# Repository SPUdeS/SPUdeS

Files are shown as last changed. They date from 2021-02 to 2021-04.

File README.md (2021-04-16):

<div id="SPUdeS">
    <h1>
         <span>
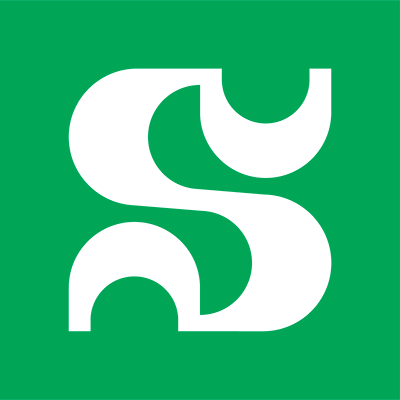
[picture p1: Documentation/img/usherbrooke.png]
usherbrooke
            
         </span>
         SPUdeS
    </h1>
    <h3>Stewart Platform Université de Sherbrooke</h3>
    <h3>UdeS-GRO | 65<sup>th</sup> Promotion | 2021</h3>
</div>

[//]: # (------------------------------------------------)

<div id="badges">
    

 

</div>

[//]: # (------------------------------------------------)

**SPUdeS is a six degrees of freedom Stewart Platform. 
This is an academic project by robotics engineering undergraduates at l'Université de Sherbrooke.**

<!-- TODO: Change image to be smaller and add a real image of platform -->
<div id="platform" align="center">
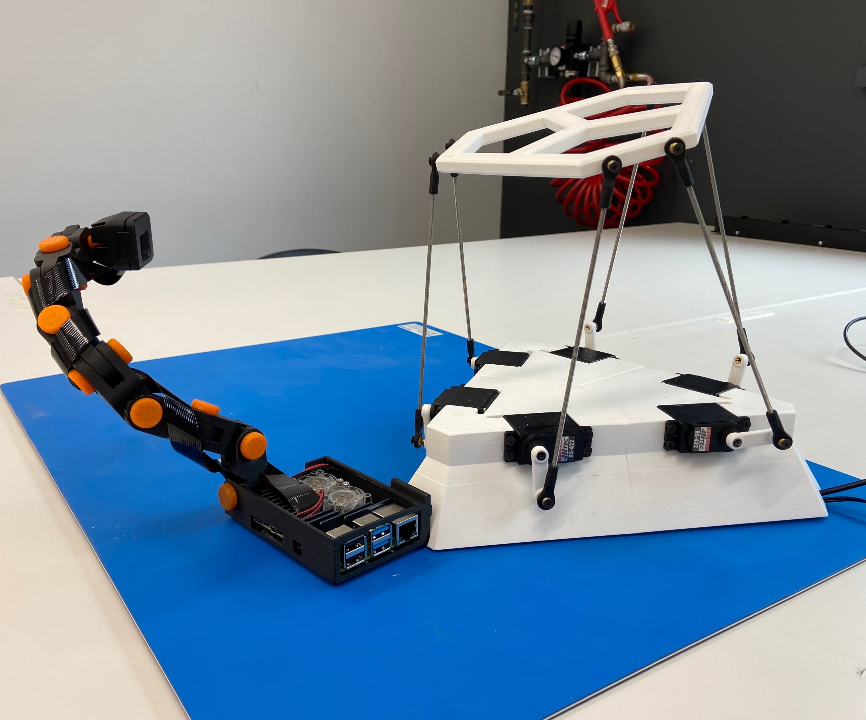
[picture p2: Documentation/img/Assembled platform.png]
Platform Assembly
    
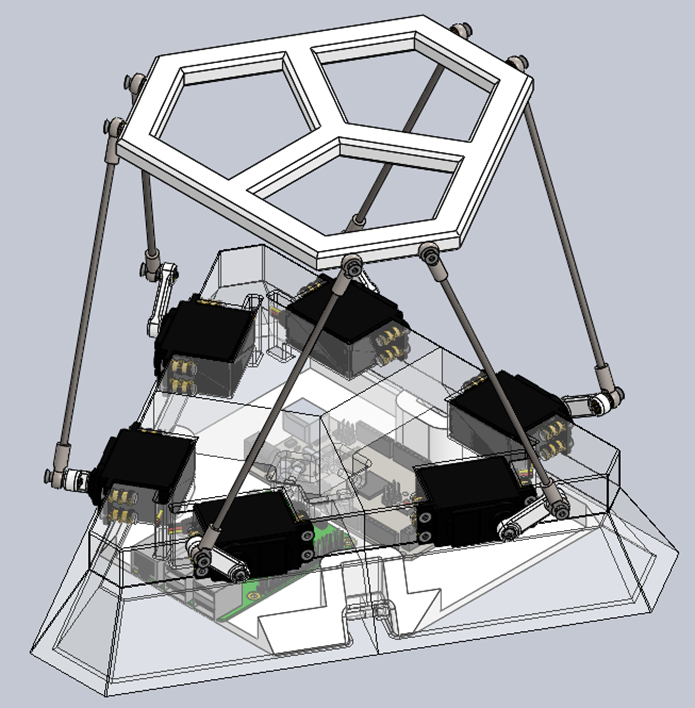
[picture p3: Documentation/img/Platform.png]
Platform Assembly
    
</div>

## Table of Contents
- **[Stewart Platforms](#Stewart)**
- **[Setup](#Setup)**
- **[Supplies](#Supplies)**
    - **[Single-Board Computer](#Computer)**
    - **[Microcontroller](#Controller)**
    - **[Servomotors](#Servo)**
    - **[Power Adaptor](#Power)**
    - **[Threaded Rods](#Rods)**
    - **[Heim Joints](#Joints)**
    - **[Hardware](#Hardware)**
    - **[Parts to solder](#Parts_solder)**
    - **[Parts to print](#Parts_print)**
- **[Platform Assembly Guide](#Assembly)**
    - **[Design](#Design)**
    - **[CAD Files](#CAD)**
    - **[Platform](#Platform)**
    - **[Base](#Base)**
    - **[Servo motor arms](#Servo)**
    - **[Legs](#Legs)**
    - **[Microcontroller holder](#Holder)**
    - **[Summary](#Summary)**
- **[Electrical Connection Guide](#Electrical)**  
  - **[Protoboard Soldering](#Proto)**
  - **[Soldering Recommendations](#Soldering)**
- **[Software Installation Guide](#Software)**
  - **[Machine requirements](#Machine_requirements)**
  - **[Cloning the Repository](#Cloning_the_Repository)**
  - **[Installing the requirements](#Installing_the_requirements)**
  - **[Running the server](#Running_the_server)**
- **[Arduino Setup Guide](#Motor_control)**
  - **[Arduino Communication Protocol](#Coms)**
  - **[PWM Precision](#PWM)**
- **[User Interface](#Operation)**
  - **[Camera](#Camera)**
  - **[Input](#Input)**
  - **[Graphical Representation of the Platform](#Graph)**
- **[License](#License)**  
 
[//]: # (------------------------------------------------)

## Stewart Platforms
A Stewart platform is a type of parallel robot built in such a way as to offer six degrees of freedom. 
This type of platform was created and publicised in the second half of the 20th century by three different engineers. 
Distributing the load on six legs allows for a strong manipulator while preserving high precision in movements. 
The combination of high strength and precision in six degrees of freedom makes this type of robot the ideal platform for various simulators (automobile, aviation). 
This type of robot as also been used for a telescope and tire testing machines.

Fundamentally, the platform is built from six linear actuators in parallel. 
Each ends of the linear actuators are linked to the fixed base and the manipulator via Heim joints. 
It is also possible to assemble the platform with rotary actuators. 
The rotation of an arm connecting to the base of the leg allows for some variation of the effective length of the legs emulating a linear actuator.
It is the way we have decided to build our prototype platform since servo motors are cheaper and easier to get our hands on then linear actuators.

## Setup
1. Acquire the components in the **[Supplies](#Supplies)** section.
2. If needed, adapt the [CAD models](CADs) of the [base](CADs/Base.SLDPRT), the [platform](CADs/Platform.SLDPRT) and the [servo arms](CADs/Legs.SLDASM) to your specific dimensions.   
2.1. If you modified the [CAD models](CADs) regenerate the [3D printing files](CADs/V2%-%HS422/3D%printing%files).
3. 3D print the platform using the [3D printing files](CADs/V2%-%HS422/3D%printing%files). This may take several days.
4. Follow the **[Platform Assembly Guide](#Assembly)** to assemble the 3D printed parts. This requires the **[Supplies](#Supplies)**.
5. Follow the **[Electrical Connection Guide](#Electrical)** to solder the protoboard.
6. Follow the **[Software Installation Guide](#Software)** to set up the server and the user interface.
7. Follow the **[Arduino Setup Guide](#Motor_control)** guide to upload the [``StandardFirmata.ino``](SPUdeS/Arduino/StandardFirmata/StandardFirmata.ino) file to the Arduino.
8. Set up the *[Raspberry Pi](#Computer)* or a computer by connecting it with the *[Arduino](#Controller)*, your computer and to a power source.
9. Commands can be sent to the platform using the user interface. Refer to the **[User Interface](#Operation)** section for more information.

## Supplies
### Single-Board Computer
- Brand: *[Raspberry Pi](https://www.raspberrypi.org/products/raspberry-pi-4-model-b/)*
- Model: Raspberry Pi 4 Model B
- Quantity: 1

### Microcontroller
- Brand: *[Arduino](https://store.arduino.cc/mega-2560-r3)*
- Model: Mega 2560 REV3
- Quantity: 1

### Servomotors
- Brand: *[Hitec RCD](https://hitecrcd.com/products/servos/sport-servos/analog-sport-servos/hs-422/product)*
- Model: HS-422
- Quantity: 6

### Power Adaptor (5V, 6A)
- Brand: *[CUI Inc.](https://www.digikey.com/en/products/detail/cui-inc/SWI10-5-N-P5/6618696)*
- Model: SWI10-5-N
- Quantity: 1

###  Threaded Rods
- Brand: *[uxcellM3](https://www.amazon.ca/gp/product/B01M9D4ASU/ref=ppx_yo_dt_b_asin_title_o08_s00?ie=UTF8&psc=1)*
- Model: a16071500ux0035
- Quantity: 6

###  Heim Joints
- Brand: *[Que-T](https://www.amazon.ca/gp/product/B08217LDWH/ref=ppx_yo_dt_b_asin_title_o07_s00?ie=UTF8&psc=1)*
- ASIN: B08217LDWH
- Quantity: 12

###  Hardware
-	Threaded inserts M3 x 6mm (42x; optional)
-	Countersunk bolts M3x6 (6x; optional)
-	Countersunk bolts M3x12 (42x)
-	Nylock nuts M3 (6x)
-	Round head self-tapping screws No3 (6x)

###  Electrical Parts
- Proto-board (1x)
- Pin / Female headers (6x)
- Wires 
- Soldering iron and solder
     
###  Parts to print
There are four parts to print: the [platform](CADs/V2%20-%20HS422/Platform.SLDPRT), 
the [base](CADs/V2%20-%20HS422/Base%20V3.SLDPRT), 
the [microcontroller holder](CADs/V2%20-%20HS422/MicroController%20Holder.SLDPRT) 
and the [servo arms](CADs/V2%20-%20HS422/ServoArm.SLDPRT). 
Materials needed:
- A spool of PLA
- Access to a 3D printer

## Platform Assembly Guide
### Design
The main components of the robot are the base, the arms fixing the legs to the servo motors, the legs themselves, and the platform. 
The geometry and proportions of the platform are critical factors allowing the position of the manipulator to be completely defined. 
Furthermore, using rotary actuators elevate the complexity versus using simple actuators. 
Thankfully, Robert Eisele has proposed and published a solution for the inverse kinematics of the platform using rotary actuators. 
Building from his *[work](https://www.xarg.org/paper/inverse-kinematics-of-a-stewart-platform/)*, it is possible to develop a custom sized platform given we respect some parameters. 
For those of you who would want to change the values we used be sure to look at the parameters defined in the configuration files of the project. 
We would strongly advise also trying your new parameters in the CAD files to inspect proportions and overall look. 
We have drawn them based on variables to make it easy for the user to input whatever values desired for the basic parameters.

To keep the project as simple as possible, we have designed the platform to be table-top sized. 
This way, it is not too small so that the hardware is easily available at the hardware store. 
On the other hand, it is not too big, so the cost of material isn’t prohibitive either. 
For maximum flexibility we based all our design on the fact that a 3D printer was readily available. 
One could use other ways to build the platform out of different materials, but we felt 3D printing was the more practical means of fabrication for most.

### CAD Files
First of all, you’ll find two version of the platform. The version one being a prototype with smaller servo motors. 
We’ve moved on from that design to upgrade to [better motors (HS-422 model)](CADs/V2%20-%20HS422). 
Those motors are more powerful limiting the impact of friction in the Heim joints at both ends of the legs. 
Note that the [CAD files of the first version](CADs/V1%20-%20SG90%20-%20Deprecated) aren’t based on variables lengths and dimensions aren’t defined the same way as the second version. 
This is important since the values in the configuration file of the main program are based on the second version’s way of dimensioning the platform. 
A reader that would want to build the first platform would have to manually measure (in the CAD software) some of the variables to update the [``configuration files``](SPUdeS/Platform/config.py) variables. 
As stated earlier, the brass inserts are optional. But if not using them, don’t forget to adjust the size of the holes where bolts will be threaded. 
Using M3 bolts, we’d recommend holes about a quarter to half a millimeter less in diameter to allow the thread to grip well on the plastic. 
The exact size depends on the precision of the printer used and orientation of the print; this I just a recommendation and testing should be done before hand.

### Platform
The word platform in its general sense describes the project in whole (Stewart Platform). 
But we also use the term to refer specifically to the upper part of the robot. 
It is a way to distinguish it from the base and the legs. 
[The platform](CADs/V2%20-%20HS422/Platform.SLDPRT) is one of the simplest parts of the project. 
It is also one that allows for lots of customization. 
This piece could be redesign to whichever shape is desired while keeping in mind that the more weight is added at the top, the greater the load placed on the servos is. 
The only other thing to keep in mind would be to try keep the anchors in the general vicinity of the anchors of the base. 
That way, in the home position, the legs are as upright as possible and allow for better movement. 
The usage of rotary actuators to lift the legs up creates a plane in which the servo arms operate. 
Since the [Heim joints](CADs/V2%20-%20HS422/Rod%20End) have an angular limit on the movement they allow, starting with upright legs effectively put the interior portion of the join at 90 degrees to the leg itself and allows for the greatest range of motion.

Printing the model provided needs no support and will take about 4 hours. 
This time is only provided as an indication since lots of parameters can impact the printing time (we used a standard layer height of 0.20 mm, 3 horizontal walls, 4 vertical walls and a 15% gyroid infill). 
For the assembly it is really simple, only install the threaded inserts press-fit in the six anchor holes. 
This is where the upper part of each leg will attach. Note that inserts are optional as stated earlier, but don’t forget to resize the anchor holes properly. 

### Base
[The base](CADs/V2%20-%20HS422/Base%20V3.SLDPRT) is the longest part to print and the more complex part of the build. 
Most of the assembly starts here and the operation of the platform is heavily linked to the geometry of this part. 
That is to says, if the platform is a part which allows for creativity, the base isn’t so much. 
For someone who would like to play with the fundamental geometry of the base we’d strongly advice to look attentively at the paper provided in reference (solution for the inverse kinematics of a servo motor operated Stewart platform by Robert Eisele). 
For others that would only like to resize the project, this is facilitated by the variables included in the CAD files. 
Note that the measurements of the motors are also variables, so it is also possible to change the motors for bigger or smaller projects without having to redraw the base. 
Just don’t forget to adjust the value of the parameters contained in the configuration file so the computation is accurate for your new dimensions. 
The printer used for our version was the Pruas Mini+ which has a build volume of 18 cm x 18 cm x 18 cm, for this reason the base is [split in three parts](CADs/V2%20-%20HS422/Base%20V3-Split.SLDPRT). 
The undivided part is also available for people using printers with bigger build volumes or is downsizing the platform results in not enough space to bolt the different pieces together. 
We suggest printing the parts up-side down. 
Leveraging the draft angle of the design and the overhang capabilities of the printer to our advantage to reduce support to its minimum saves more then an hour per piece (a third of the base). 
If your bridging parameters are well dialed-in, the part can be printed as is in the upside-down orientation. 
Otherwise, the part needs some supports that you can apply to the faces where the servo motors lie. 
Since there’s minimal support needed, the print time added is negligeable and we’d suggest taking this route since in the end the surface will look better, and it is probably not worth risking disappointing surface finish only to save couple of minutes on a ten plus hours print. 
With three walls and the rest of the parameters the same, it takes about 30-32 hours in total to complete printing the base. Don’t forget to resize holes if not using the inserts.

To assemble the platform, follow those steps:
1.	Fix the three parts of the base together with the M3x16 mm bolts (6) and the nylon locknuts (6). Holes for the bolts and to fix the nut in place are located underneath the base. \
&nbsp;&nbsp;&nbsp;&nbsp;&nbsp;&nbsp; a.	Be sure to tighten enough so that the parts do not have room to move relative to each other.\
&nbsp;&nbsp;&nbsp;&nbsp;&nbsp;&nbsp; b.	The nut may start to turn within the hexagonal hole where it’s located because of the friction of the nylon transferring the torque of the bolt. Wedging a small flat head screwdriver or a small Exacto blade helps retain the nut in place while tightening the bolt.
2.	Install the inserts that allow for the servos to be fixed. Note that four inserts are more then required for the application but since we had them, and the servo used had four holes to fix them we used them all. This is not optimal in any way nor is it required.
3.	Pass the wires of the servo motors through the holes in the base and slide the motors in place.
4.	Install the bolts to fix the servos.

### Servo motor arms
The [servo arms](CADs/V2%20-%20HS422/ServoArm.SLDPRT) are the parts that requires the less time for the print and are simple to assemble. 
The bridging parameters will impact the looks of one side of the arm, printing toothed side-down will allow the better-looking side to be facing out at installation (surface irregularities due to the bridging end up on the base-facing side of the arm). 
Printing the 6 servo arms at once will only take about one hour. 
We advise using the same general parameters but increasing the number of walls (increasing the infill percentage doesn’t have as much impact). 
That way, the arms are sturdier and print time isn’t that much longer. 
Once printed, install the threaded insert in the round hole, then install the toothed side onto the servo motor shaft. Do not push hard on the shaft towards the servo motor, it could damage the motors. 
Instead, put the arm in place and gently screw it in place. The self-tapping screw will thread into the plastic shaft pulling the arm on its way. 
When placing the arms, be sure that the range allowed by the servos (about 180 degrees) span the bottom to the top of the base and faces the exterior. 
This allows the leg to have a full range of motion from the lower point to the highest point of the arc made by the rotation of the arm. 
In the configuration used we like the arms to be outside facing but inside would be another working configuration (all arms must be the same in one or the other configuration).

### Legs
The legs are simply the [female Heim joints](CADs/V2%20-%20HS422/Rod%20End) threaded at both ends of the [150 mm rods](CADs/V2%20-%20HS422/Tige%20filetée.SLDPRT). 
Be sure to them facing approximately in the same direction so that the range of motion isn’t hampered. 
Then it is just a question of fixing the legs to both the base and the platform using the M3 blots. 
The major triangle in the base and the platform should be inverted as shown in the image. 

### Microncontroller holder
The positioning of the microcontrollers is up to you. 
The [holder](CADs/V2%20-%20HS422/MicroController%20Holder.SLDPRT) piece doesn’t have holes in it. 
Depending on the type of different microcontroller used to drive the platform, bolt patterns may vary. 
For this reason, we suggest marking drilling holes at the location you want to place the microcontrollers on the holder. 
Then it is only a question of installing the inserts (drill a hole smaller than the insert diameter to allow for a press-fit in the plastic) and using small M3x6 mm bolts to fix the microcontrollers. 
The holder should snap in place beneath the base. 

### Summary
Printing all the pieces required for the build takes about 560 grams of PLA which is a bit more than half a spool. 
Accounting for three quarters to an entire spool’s (1 kg) worth of PLA is advisable for someone who’d want to do tests to optimize surface finish. 
The pictures shown below illustrate how the principal components are fastened to the platform (in this case, the base is in one piece but the three-pieces model is assembled in the same way).

<div id="platform" align="center">
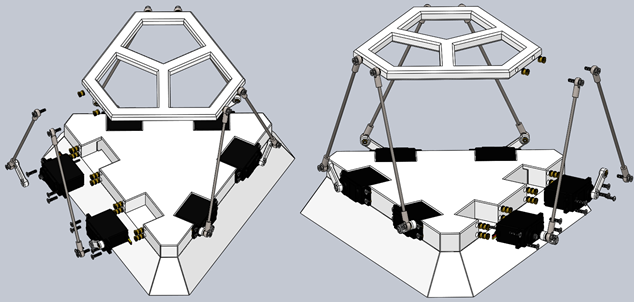
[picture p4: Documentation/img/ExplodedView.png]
    
</div>

Now it is only a question of uploading the codes to the Arduino and the raspberry pi and connecting both with the appropriate power adaptors. 
Launching the web server allows for a clean interface where the user can command the platform.

## Electrical Connection Guide
### Protoboard Soldering
This section makes reference to the [electrical schematics](Documentation/Electical%20schematics.pdf).The electrical part of the assembly requires you to solder a protoboard. 
-	Solder two female pin headers to the protoboard. This will be used for the power supply by connecting two male connectors; one for the ground and one for the VCC.
-	Solder 6 short wires to the protoboard’s positive (VCC) side. These will be used on the positive side of each motor.
-	Solder 7 short wires to the protoboard’s ground side. These will ground each motor and the Arduino.
-	Each of the motors will need an additional wire to plug into the digital pin of the Arduino. 

<div style="text-align: center;">
  <table style="margin: 0px auto">
    <tr>
      <td> Motor 1 </td>
      <td> Motor 2 </td>
      <td> Motor 3 </td>
      <td> Motor 4 </td>
      <td> Motor 5 </td>
      <td> Motor 6 </td>
    </tr>
    <tr>
      <td> Pin 7 </td>
      <td> Pin 9 </td>
      <td> Pin 11 </td>
      <td> Pin 12</td>
      <td> Pin 5 </td>
      <td> Pin 3 </td>
    </tr>
  </table>
</div>

### Soldering Recommendations	
The motor positioning is important so be careful when plugging them. Here are some tips you can use:
-	Soldering will be simpler if you minimise the distance between the components.
-	Be careful to not touch the protoboard.
-	It can be useful to use more solder than usual.

## Software Installation Guide
The interface was build using the Python micro framework Flask. We built our webpage using html and handle our requests by using Javascript functions and route handling on the server side.
###  Machine Requirements
Our project runs on specific versions of Python:
- [``Python 3.7``](https://www.python.org/downloads/release/python-3710/)
- [``Python 3.8``](https://www.python.org/downloads/release/python-389/)
- [``Python 3.9``](https://www.python.org/downloads/release/python-394/)

[``pip3``](https://pip.pypa.io/en/stable/) is also required to install the project's various packages.
### Cloning the Repository
Let us start the installation by cloning the repository. 
You may choose to do this via the Github Desktop App or through some code versioning software such as Sourcetree or Square Desktop. We will use Git in a terminal. 
If you haven't already, download [``Git``](https://git-scm.com/downloads).
Start by entering into the folder you want the project to be in and open up a terminal. Next use the following command to clone the repository.
```shell
git clone https://github.com/SPUdeS/SPUdeS.git
```
### Installing the requirements
Now you will need to install the modules and packages needed to run the server. Go ahead and run this next command.
```shell
pip3 install -r requirements.txt
```
The [``requirements.txt``](requirements.txt) file is what lets you download all the dependencies for the project.
If you get an error where an import is missing, please install it manually. For example, to download OpenCV manually you will open back up that terminal window and write the following.
```shell
pip3 install opencv-python
```
If you are using a Raspberry Pi and are still having issues with OpenCV, *[this link](https://stackoverflow.com/questions/53347759/importerror-libcblas-so-3-cannot-open-shared-object-file-no-such-file-or-dire)* may be helpful.
### Running the server
Starting from the root of the repository, run the server with this command.
```shell
python3 SPUdeS.py
```
To see the interface webpage visit *[this address](http://127.0.0.1:5000)* on the same machine: ``http://127.0.0.1:5000`` 

## Arduino Setup Guide

### Arduino Communication Protocol
To control the servo motors, we use a microcontroller, the *[Arduino Mega 2560](#Controller)*. 
Since the angles we need to send to the servos are calculated in our inverse kinematics python code, we chose to communicate directly from a python program to the Arduino. 
This is done using the open source *[pyFirmata library](https://github.com/tino/pyFirmata)*, which applies the *[Firmata protocol](https://github.com/firmata/protocol)* for communication with microcontrollers. 
To use this protocol, we simply need to send the [``StandardFirmata.ino``](SPUdeS/Arduino/StandardFirmata/StandardFirmata.ino) file to the Arduino and import the pyFirmata library into our program.

We created a class, [``ard_communication``](SPUdeS/Arduino/ard_communication.py) that applies this concept. 
There are two ways to use it, the first being to simply run it and use its functions in the main, a way that was mostly used to test the motor movements with preprogrammed trajectories and manual inputs. 
The second way is to initialize an instance of the class in our server, and then use its functions there, as we did with our end to end project. 
Its main function is setServoAngle, which receives an array of n arrays of 6 angles, one for each motor. 
It can take angles in degrees and radians, depending on the parameter isRad, which will make sure to correct the angles so they are sent in degrees to the Arduino.

For now, the class uses the digital pins of the Arduino in their pyFirmata.SERVO mode, which makes it so we can send angles in degrees to the Arduino, and it will convert it to a corresponding voltage in PWM to the servos. 
This has some drawbacks, such as a loss in precision of the angles since the digital.write function requires integer values. 
Also, the discretization of the trajectory can look somewhat choppy because the program needs to sleep for a certain amount of time before sending a new angle, otherwise it will miss some waypoints.

### PWM Precision
This brings us to the next step for the motor control aspect of the project. 
There is a possibility to change the digital pins' mode to pyFirmata.PWM and change the file uploaded to the Arduino with a modified version of 
example file *[simpleAnalogFirmata](https://github.com/grappendorf/arduino-framework/blob/master/Firmata/examples/SimpleAnalogFirmata/SimpleAnalogFirmata.ino)*. 
[Our implementation of this file](/SPUdeS/Arduino/PWMFirmataBeta/PWMFirmataBeta.ino) was still in beta and not ready for use with our [ard_communcation](SPUdeS/Arduino/ard_communication.py) module. 
The goal of these changes is to change from an 8 bit resolution PWM to a 16 bit resolution PWM and get rid of the integer restriction of the digital.write function. 
With a few changes, this could allow much more precision in the platform's movements, but might reduce the refresh rate of the PWM, which could cause other issues. 
It is still the next step for motor control since precision is crucial for a Stewart's platform. 
Though it was not needed yet for our implementation of the platform since it currently has no real function and the standard Firmata file with the SERVO mode for the Arduino's pins are enough for our proof of concept.

## User Interface
The user interface (UI) is implemented using [this html file](SPUdeS/PythonUI/templates/index.html). 
We used *[Bootstrap](https://getbootstrap.com)* to format the webpage and Javascript to handle requests.
The user interface can be split into three main parts:
- The Camera
- The User Input
- The Graphical Representations of the Platform

<div align="center">
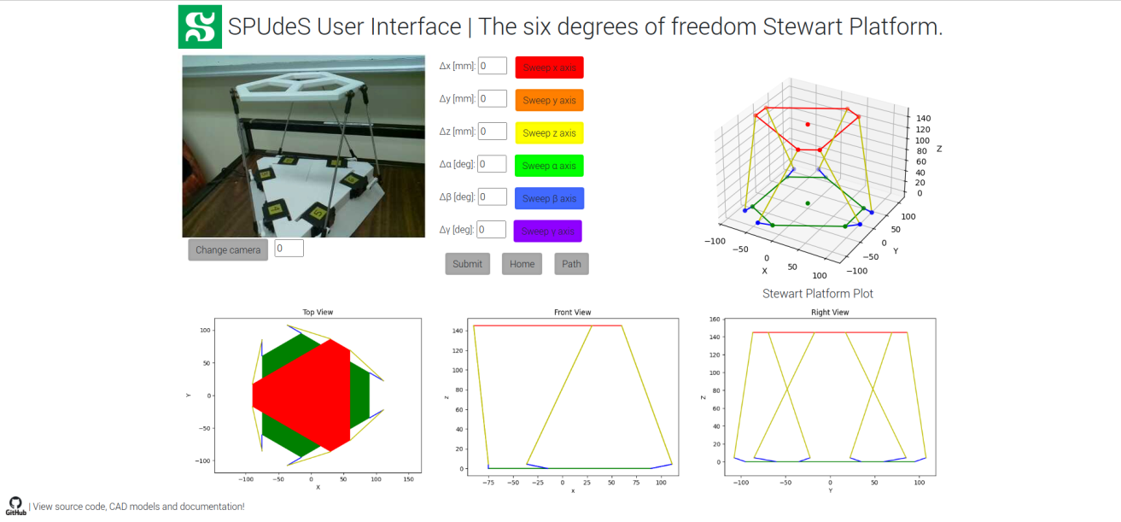
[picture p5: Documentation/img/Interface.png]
Interface
    
</div>

### Camera
The camera was implemented to show the platforms movements live through the UI. 
We used *[OpenCV](https://opencv.org)* to implement the live video feed.
We have tested the use of a laptop webcam and a Raspberry Pi camera. Both have worked 
successfully. There is a button and input that allow you to change the port of the 
camera being used. 

<div align="center">
  CameraButton
</div>

### User Input
Firstly we have inputs for specific positions of different axes possible. 
To use these enter a value in as many of the boxes and hit the button Submit. 
This sends the request to the server to sent to the platform and the update of the graphs. 
Secondly we have the sweep buttons for each axis. These are preprogrammed paths to show the range of motion on that specific axis. 
Clicking the corresponding axis button submits the request. 
Thirdly there is a button for homing the platform at a predetermined angle specified in [ard_communication](SPUdeS/Arduino/ard_communication.py). Lastly there is a button called Path that performs a combination of all the sweep movements.

<div align="center">
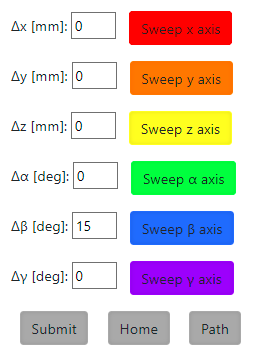
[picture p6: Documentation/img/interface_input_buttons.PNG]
InputButtons
    
</div>

The push of a button calls a Javascript function that creates a new XML HTTP Request. 
Some Javascript functions create a json payload of the type of displacement called and the position that is sent. 
The function then POSTs and calls the route used in the Flask server. 
From the server side we are able to handle the request by using payload in a cinematic function. 
We then send a response to motors and an update of the graph.

### Graphical Representation of the Platform
The graphical representation is updated using the [``stewartPlatform.py``](SPUdeS/Platform/stewartPlatform.py) which uses *[matplotlib](https://matplotlib.org)* to represent the platform graphically. 
The same input used to send the movement command to the motors is used to created an updated graph. 
However the graph does not update automatically on the interface. The user needs to use F5 or CTRL+F5 to update the graphs on the UI.

<div align="center">
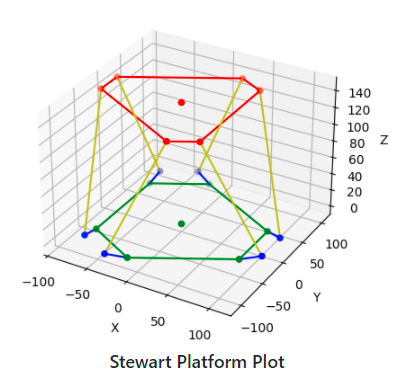
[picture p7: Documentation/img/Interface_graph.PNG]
Graph
  
</div>

There are other views of the platform included at the bottom of the interface for a better visual of the movement sequence.

## License
This project is licenced under a   license.
This license ensures the community can use, modify and share our project.

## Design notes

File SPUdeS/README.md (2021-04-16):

#  Module `SPUdeS`
## Sub-modules

* [SPUdeS.Arduino](#SPUdeS.Arduino)
* [SPUdeS.Platform](#SPUdeS.Platform)
* [SPUdeS.PythonUI](#SPUdeS.PythonUI)

#  Module `SPUdeS.Arduino`

## Sub-modules

* [SPUdeS.Arduino.ard_communication](#SPUdeS.Arduino.ard_communication)

#  Module `SPUdeS.Arduino.ard_communication`

## Classes

###  Class `ard_communication`

>     class ard_communication

The ard_communication class handles all the communication protocol between the Arduino and the Python
functions using the library pyfirmata.

The __init__() function sets up the connection to the Arduino via USB, it initializes the Motor to Pin
connections and some basic set up angles (min, max, homing angles). This function also calls the
setUpMotors() function to initialize the motor connections with the Arduino. It finally calls the
gotoHomePosition() function which sends the homing angles command to the motors.

#### Methods

#####  Method `goToHomePosition`

>     def goToHomePosition(
>         self
>     )

The goToHomePosition() function calls the setServoAngle() function with the arguments of the homing angles
initialized in the __init__().

#####  Method `setServoAngle`

>     def setServoAngle(
>         self,
>         angle,
>         isRad=1
>     )

The setServoAngle() function receives a set of arrays with each 6 elements. The sets of angles are for
sending small movements to the motors and the 6 elements in each array are the angles for each one of the
motors. There is also an option for sending the list of angle arrays in radian or not. By default,
we assume that the angles are in radians.

#####  Method `setUpMotors`

>     def setUpMotors(
>         self
>     )

The setUpMotors() function initializes the pin connections to the servo motors.

#  Module `SPUdeS.Platform`

## Sub-modules

* [SPUdeS.Platform.config](#SPUdeS.Platform.config)
* [SPUdeS.Platform.kinematicFunctions](#SPUdeS.Platform.kinematicFunctions)
* [SPUdeS.Platform.stewartClasses](#SPUdeS.Platform.stewartClasses)
* [SPUdeS.Platform.stewartPlatform](#SPUdeS.Platform.stewartPlatform)

#  Module `SPUdeS.Platform.config`

Configuration file to define the geometry of the platform.
This file contain the relevant information to perform the inverse kinematics computations.
If the platform geometry is changed, then this file should be modified and everything else
should stay the same in the stewartPlatform file.

#  Module `SPUdeS.Platform.kinematicFunctions`

This module defines various kinematic functions used in the stewartClasses and the stewartPlatform.

## Functions

###  Function `getAlpha`

>     def getAlpha(
>         effectiveLegLength,
>         beta,
>         base,
>         platform
>     )

Computes servo angle as a function of the platform orientation and position,
the leg's effective length and it's angle beta (angle between servo arm and base x-axis).

###  Function `getAnglesFromRotationMatrix`

>     def getAnglesFromRotationMatrix(
>         b_R_p
>     )

Computes Yaw, pitch, roll from rotation matrix b_R_p.
Convention: Euler ZYX (α,β,γ).

###  Function `getNumberOfWaypoints`

>     def getNumberOfWaypoints(
>         initialOrigin,
>         initialVectorBase,
>         targetOrigin,
>         targetVectorBase
>     )

Returns the number of samples.
Distance to travel sampled at a rate defined by config variable pathSamplingPrecision.

###  Function `getRotationMatrix`

>     def getRotationMatrix(
>         vb1,
>         vb2
>     )

Computes the rotation matrix between two vector bases.
Convention: Euler ZYX (α,β,γ).

###  Function `getRotationMatrixFromAngles`

>     def getRotationMatrixFromAngles(
>         alpha,
>         beta,
>         gamma
>     )

Sets the rotation matrix needed given yaw, pitch and roll.
Based on Yaw, pitch, roll - Euler ZYX(alpha, beta, gamma) convention.
platform unitvectors are given as: [[Px],[Py],[Pz]] in reference frame Base
alpha = angle around z
beta = angle around y
gamma = angle around x

#  Module `SPUdeS.Platform.stewartClasses`

This file contains the building blocks of the stewartPlatform class.
Contains the frame, _piece, base and platform classes.

## Classes

###  Class `base`

>     class base(
>         origin=[0, 0, 0],
>         vectorBase=array([[1, 0, 0],
       [0, 1, 0],
       [0, 0, 1]])
>     )

This class defines the properties of a base piece. Extends _piece class.
This class is instantiated in the stewartPlatform class.

#### Ancestors (in MRO)

* [SPUdeS.Platform.stewartClasses._piece](#SPUdeS.Platform.stewartClasses._piece)
* [SPUdeS.Platform.stewartClasses.frame](#SPUdeS.Platform.stewartClasses.frame)

###  Class `frame`

>     class frame(
>         origin,
>         vectorBase
>     )

Position : column vector describing position in Base Frame
Unit vectors [[Nx],[Ny],[Nz]] where Nx,y,z are column vectors
representing unitvectors of the frame in the Base reference frame

#### Descendants

* [SPUdeS.Platform.stewartClasses._piece](#SPUdeS.Platform.stewartClasses._piece)

#### Methods

#####  Method `getOrigin`

>     def getOrigin(
>         self
>     )

#####  Method `getVectorBase`

>     def getVectorBase(
>         self
>     )

#####  Method `setOrigin`

>     def setOrigin(
>         self,
>         origin
>     )

#####  Method `setVectorBase`

>     def setVectorBase(
>         self,
>         vectorBase
>     )

#####  Method `updateFrame`

>     def updateFrame(
>         self,
>         newFrame
>     )

###  Class `platform`

>     class platform(
>         linkedBase,
>         origin=[0, 0, 0],
>         vectorBase=array([[1, 0, 0],
       [0, 1, 0],
       [0, 0, 1]])
>     )

This class defines the properties of a platform piece. Extends _piece class.
This class is instantiated in the stewartPlatform class.

#### Ancestors (in MRO)

* [SPUdeS.Platform.stewartClasses._piece](#SPUdeS.Platform.stewartClasses._piece)
* [SPUdeS.Platform.stewartClasses.frame](#SPUdeS.Platform.stewartClasses.frame)

#### Methods

#####  Method `getAngles`

>     def getAngles(
>         self
>     )

Returns the angles of the platform based on its rotation matrix / vector base.

#####  Method `getHomeOrigin`

>     def getHomeOrigin(
>         self,
>         linkedBase
>     )

Returns home position of platform - computed from base/platform anchors #1 but any would do by symmetry.

#  Module `SPUdeS.Platform.stewartPlatform`

This file contains the stewartPlatform class. This defines the geometry of the stewart platform.

## Classes

###  Class `stewartPlatform`

>     class stewartPlatform

Contains inner classes base and platform. This defines the geometry of the stewart platform.

#### Static methods

#####  Method `confirmRequestValidity`

>     def confirmRequestValidity(
>         type_,
>         data_
>     )

Confirms whether or not the request is valid.
Returns 0 if type is target, 1 if type is sweep, and -1 if there is a problem with the request.

#####  Method `drawLinesBetweenPoints`

>     def drawLinesBetweenPoints(
>         axis,
>         listOfPointsToJoin,
>         colour
>     )

This function takes a plot and a list of points to join as parameters.
The colour parameter specifies the colour of the line to draw.

#####  Method `getTargetFrameFromPoint`

>     def getTargetFrameFromPoint(
>         targetPoint
>     )

Returns a frame for a target point.

#### Methods

#####  Method `UpdateArmPoints`

>     def UpdateArmPoints(
>         self
>     )

Initiates useful variables to plot the stewart platform.

#####  Method `display3D`

>     def display3D(
>         self,
>         updateArmPoints=False
>     )

This function plots the main 3D plot of the stewartPlatform
Redefines the 3D png plot found in the PythonUI module.
Variable updateArmPoints defaults to false and specifies if the arms are to be recalculated.

#####  Method `displayView`

>     def displayView(
>         self,
>         updateArmPoints=False
>     )

This function plots three views of the current position of the stewart platform.
Redefines the three 2D png plots found in the PythonUI module.
Variable updateArmPoints defaults to false and specifies if the arms are to be recalculated.

#####  Method `generateListOfTargets`

>     def generateListOfTargets(
>         self,
>         requestType,
>         data_
>     )

Redirects request depending on its type.

#####  Method `getArmPoints`

>     def getArmPoints(
>         self
>     )

#####  Method `getArmPointsToJoin`

>     def getArmPointsToJoin(
>         self
>     )

Helper function for the plot that defines the points that are to join for the servo arms.

#####  Method `getBasePlatformRotationMatrix`

>     def getBasePlatformRotationMatrix(
>         self
>     )

Returns the rotation matrix between the base and the platform.

#####  Method `getEffectiveLegLengths`

>     def getEffectiveLegLengths(
>         self,
>         targetFrame
>     )

Compute effective leg lengths : Effective length = T + b_R_p * Pi - Bi.

#####  Method `getLegPointsToJoin`

>     def getLegPointsToJoin(
>         self
>     )

Helper function for the plot that defines the points that are to join to the platform.

#####  Method `getListServoAngles`

>     def getListServoAngles(
>         self,
>         listOfTargets
>     )

Return a list of six-tuples servo angles to move through the trajectory.
Returns the last waypoint to later update the platform's origin.

#####  Method `getRotationAnglesToFrame`

>     def getRotationAnglesToFrame(
>         self,
>         targetFrame
>     )

Returns the rotation angle between the platform and a target frame.

#####  Method `getRotationMatrixToTarget`

>     def getRotationMatrixToTarget(
>         self,
>         targetVectorBase
>     )

Returns the rotation matrix between the base and a target frame.

#####  Method `getServoAngles`

>     def getServoAngles(
>         self
>     )

#####  Method `initHomeServoAngle`

>     def initHomeServoAngle(
>         self
>     )

This function defines the servo six servo angles at the home position.

#####  Method `inverseKinematics`

>     def inverseKinematics(
>         self,
>         targetFrame
>     )

Takes in parameters the new target frame the user wants to go to and the actual
frame (given by the object platform).
Returns servo angles necessary to accomplish the movement.
target = [x, y, z, ψ, θ, φ ] (angles d'Euler)

#####  Method `pathSampling`

>     def pathSampling(
>         self,
>         targetFrame
>     )

Return a list of waypoints to get to the target.
Each waypoint is a new frame coinciding with the new platform location
Uses precision from config file

#####  Method `requestFromFlask`

>     def requestFromFlask(
>         self,
>         type_,
>         data_
>     )

This function handles an initialization, displacement or sweep request from flask.
Returns a list of servo angles.

#####  Method `requestShowoffFromFlask`

>     def requestShowoffFromFlask(
>         self
>     )

This function handles a showoff request from flask. Defines a complex trajectory.
Returns a list of servo angles.

#####  Method `targetListForInitialize`

>     def targetListForInitialize(
>         self
>     )

Defines the list of targets in an initialization request.

#####  Method `targetListForSweep`

>     def targetListForSweep(
>         self,
>         DoF
>     )

Defines the list of targets in a sweep request.

#####  Method `targetListForTarget`

>     def targetListForTarget(
>         self,
>         displacements
>     )

Defines the list of targets in a simple displacement request.

#####  Method `updateAllPlots`

>     def updateAllPlots(
>         self,
>         updateArmPoints=True
>     )

This functions runs both plot generating function.
This has the advantage of only updating the arm points once.
Variable updateArmPoints defaults to true and specifies if the arms are to be recalculated.

#  Module `SPUdeS.PythonUI`

## Sub-modules

* [SPUdeS.PythonUI.Server](#SPUdeS.PythonUI.Server)
* [SPUdeS.PythonUI.config](#SPUdeS.PythonUI.config)

#  Module `SPUdeS.PythonUI.Server`

This Server.py file is a class called Server() that sets up the server and runs it. This is the link between the client side inputs and the cinematic
functions to send commands and new graphs.

## Classes

###  Class `Server`

>     class Server

Web server class.

The __init__ function instantiates a stewartPlatform(), an ard_communication() and
a Flask object. This function also sets up the home plot for the 3D graphs and sets up a camera. It then initializes
the routes for the Flask server and runs the server.

#### Static methods

#####  Method `initPlot`

>     def initPlot()

initPlot() refactors the 3D plots created to give us a clean slate to work with. It re-initializes the plots
to the default ones. The plots are in SPUdeS/PythonUI/static/img.

#### Methods

#####  Method `generate_frames`

>     def generate_frames(
>         self
>     )

generate_frame() function generates the frame by frame of the camera to create the live feed on the web page.

#####  Method `initiateFlaskApp`

>     def initiateFlaskApp(
>         self
>     )

The initiateFlaskApp() function calls an instance of the Flask object.

#####  Method `requestSP`

>     def requestSP(
>         self,
>         type_,
>         data
>     )

requestSP() is called through the /NewDisplacementRequest route. It uses the json payload sent from the JavaScript function to send a command in angles to the Arduino
and to update the 3D plots.

#####  Method `requestShowoffSP`

>     def requestShowoffSP(
>         self
>     )

requestShowoffSP() is called through the /NewShowoffRequest route. It calls a function to send predetermined movement commands to the Arduino
and to update the 3D plots.

#####  Method `run`

>     def run(
>         self
>     )

The run() function runs an instance of the Flask server called app.

#####  Method `updateCamera`

>     def updateCamera(
>         self,
>         cameraNumber=0
>     )

updateCamera() has by default value 0 for the number of the camera to use on the server. If a camera change is requested cameraNumber will
change to the number requested. cv2 is the imported library for OpenCV which allows us to have a live feed.

#  Module `SPUdeS.PythonUI.config`

Configuration File for the PythonUI folder. This file shares the path of PythonUI to be able to store the images
created in the kinematic functions

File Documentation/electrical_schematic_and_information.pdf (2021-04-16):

# Maximum Power current consumption check-out

The maximum power current consumption of the HS-422 is 800mA and the maximum current

consumption of the Arduino is 800mA. So, the Arduino cannot power the 6 motors, because it will

burn out therefore the external power source is needed. The total maximum current consumption

is 0.8*(6)+0.8 = 5.6 A, if we compare this value with the actual value of the adaptor(2A) we realise,

that this doesn’t work, so if we make this change we will need to find an other adaptor.

# Maximum PWM current consumption check-out

The PWM pin of the Arduino emit a constant signal between 0 and 20mA, who contain an 8bits

signal corresponding of the position send. The servo motor will have in entry the signal sends by

the Arduino and the power input/output. So, the servo motor will adjust itself for that the power

used for functionate the motor will be proportional to the angle signal and we will have the angle

desired. Therefore, the angle will be expressed in a ratio between the maximum and minimum

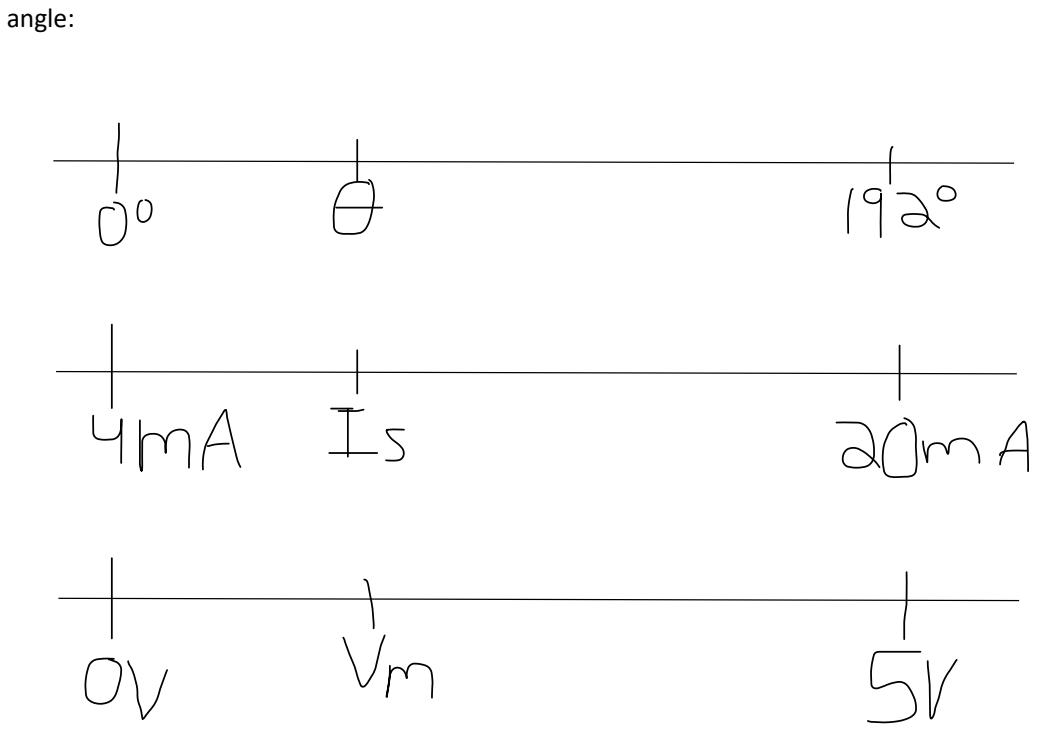
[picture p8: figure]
angle:

New Schematic

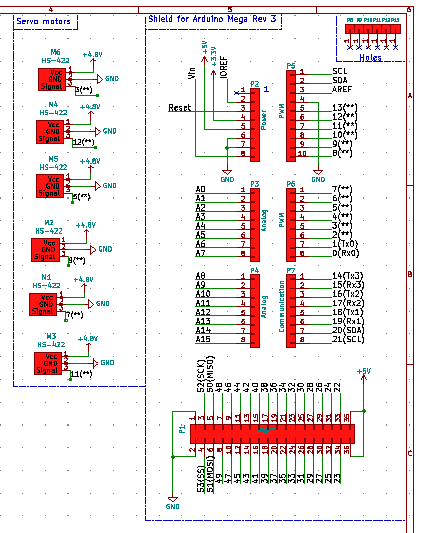
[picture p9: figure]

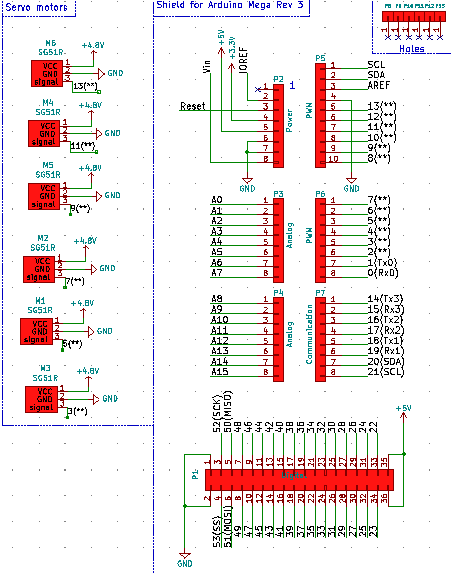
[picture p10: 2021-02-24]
Documentation/img/Electrical schematics.png

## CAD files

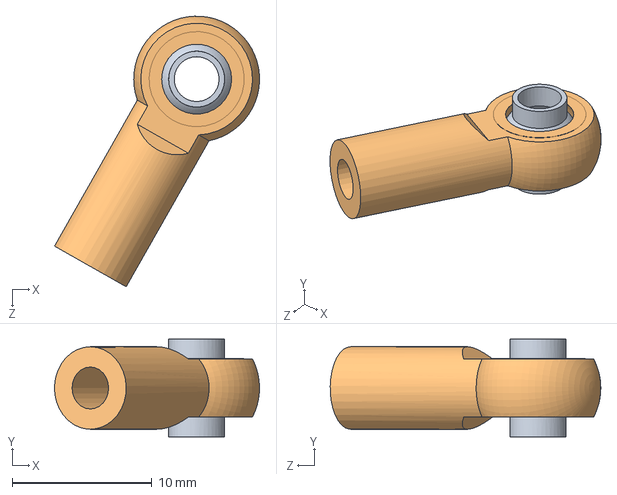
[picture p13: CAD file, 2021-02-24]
CADs/V2 - HS422/Rod End/Rod End M3.SLDASM
14.7 x 7.00 x 19.3 mm
Rod End Roller
Rod End Housing

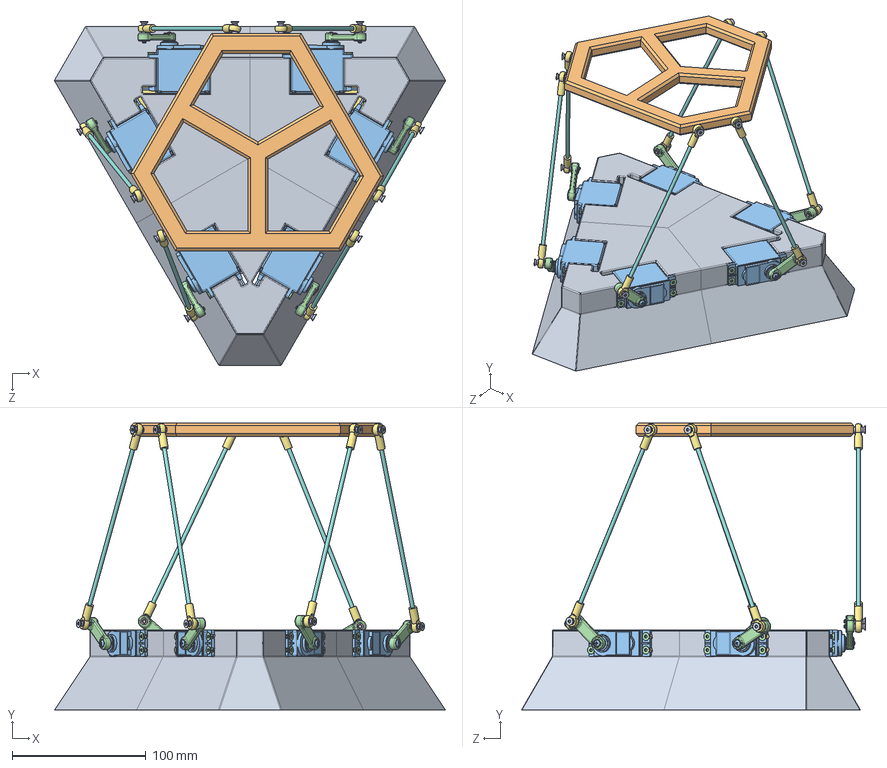
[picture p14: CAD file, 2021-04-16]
CADs/V2 - HS422/Stewart Platfrom V2.SLDASM
292.9 x 214.9 x 257.7 mm
Base V3
Threaded insert M3x10x5 x 24
hs-422_sws x 6
ServoArm x 6
Threaded insert M3x6x5 x 12
Rod End Roller x 12
Rod End Housing x 12
Tige filetée x 6
91294A134_BLACK ALLOY STEEL FLAT-HEAD SOCKET CAP SCREW x 12
Platform
No 3 - 99461A825_THREAD-FORMING SCREW FOR PLASTIC x 6
M3x12 - 91294A132_BLACK ALLOY STEEL FLAT-HEAD SOCKET CAP SCREW x 24
ArduinoMega
RASPBERRY PI 3
MicroController Holder

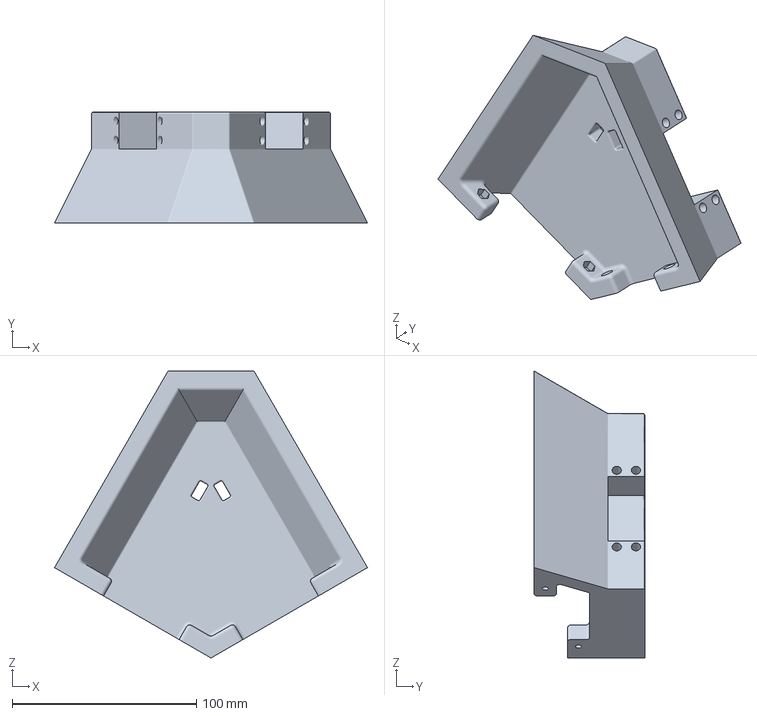
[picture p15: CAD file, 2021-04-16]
CADs/V2 - HS422/3D printing files/BaseSplit.3MF
169.9 x 60.1 x 155.8 mm

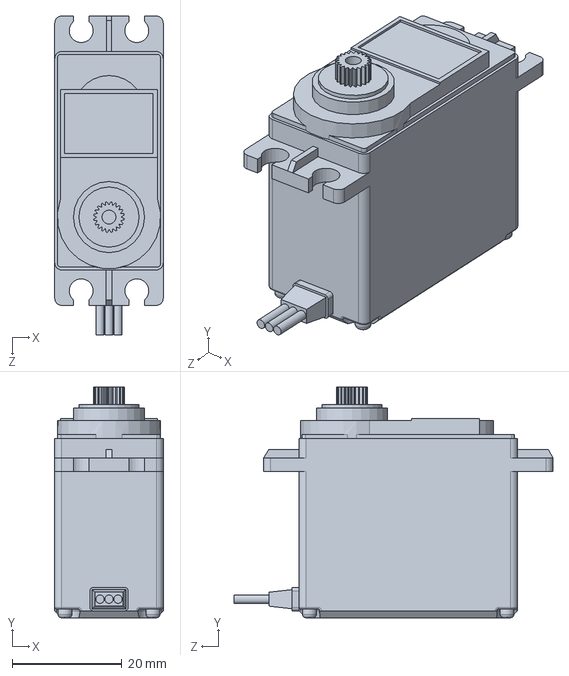
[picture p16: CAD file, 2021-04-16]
CADs/V2 - HS422/hs-422_sws.SLDPRT
19.8 x 42.1 x 58.2 mm

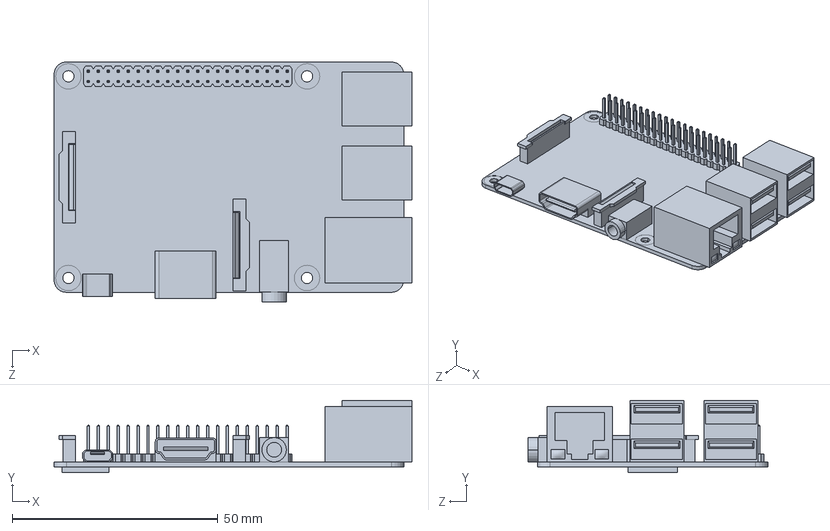
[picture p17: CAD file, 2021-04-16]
CADs/V2 - HS422/MicroControllers/RASPBERRY PI 3.SLDPRT
87.0 x 17.5 x 58.4 mm

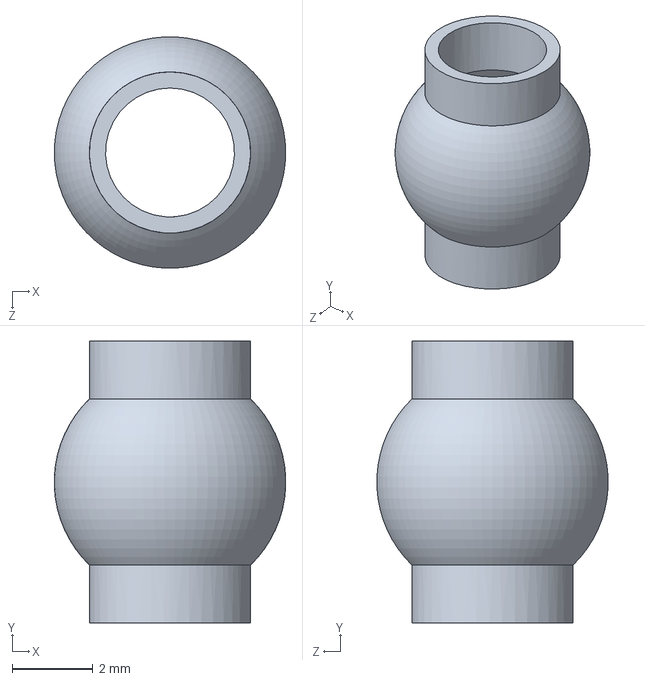
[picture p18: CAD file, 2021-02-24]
CADs/V2 - HS422/Rod End/Rod End Roller.SLDPRT
5.74 x 7.00 x 5.74 mm

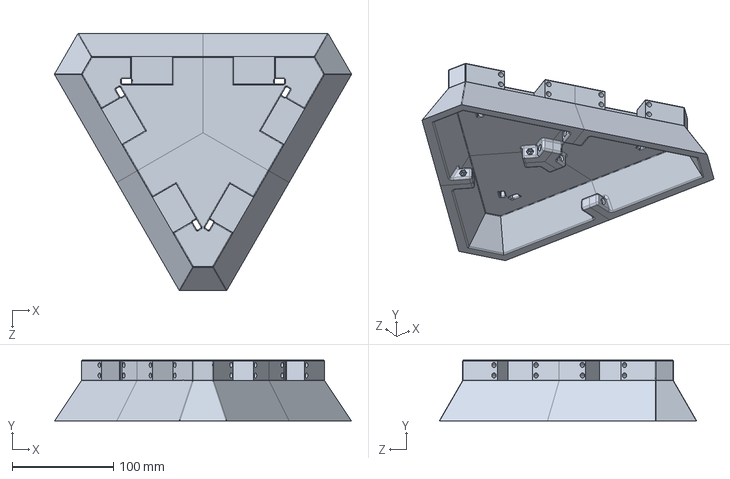
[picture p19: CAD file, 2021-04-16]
CADs/V2 - HS422/Base V3.SLDPRT
292.9 x 60.1 x 253.9 mm

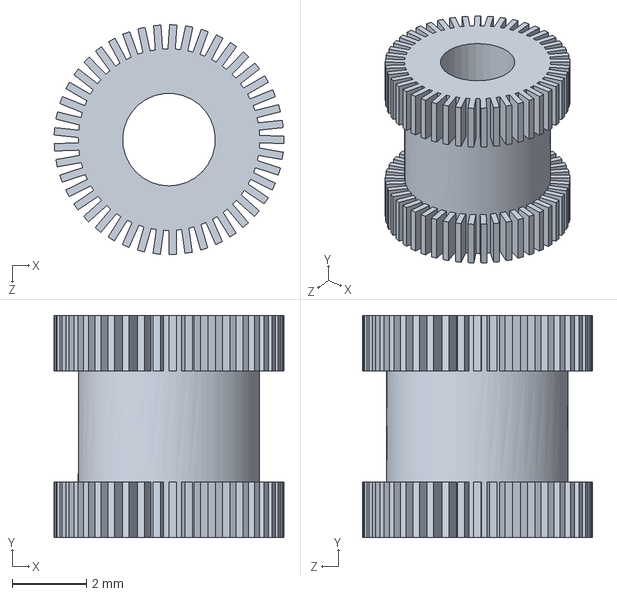
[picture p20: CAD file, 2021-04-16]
CADs/V2 - HS422/Hardware/Threaded insert M3x6x5.SLDPRT
6.21 x 6.00 x 6.21 mm

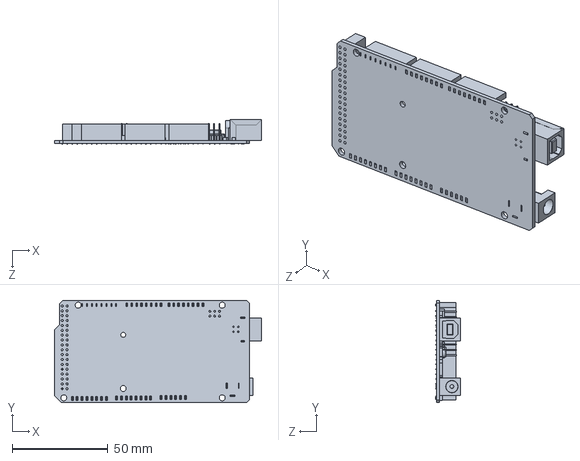
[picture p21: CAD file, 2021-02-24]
CADs/V2 - HS422/MicroControllers/ArduinoMega.SLDPRT
107.9 x 53.4 x 13.0 mm

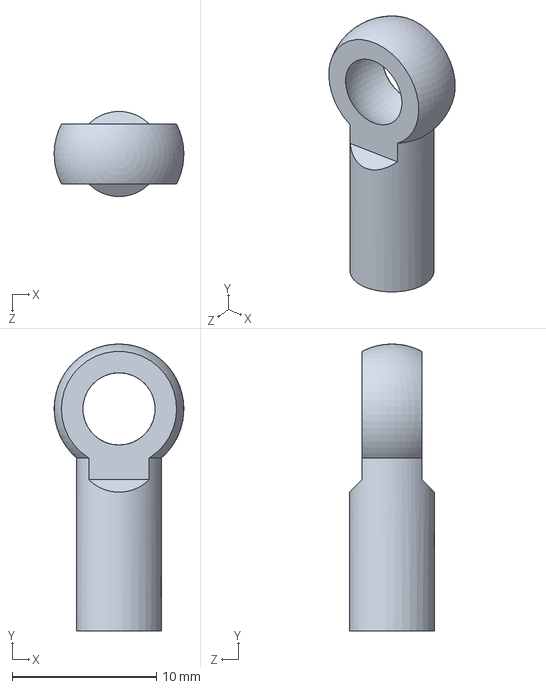
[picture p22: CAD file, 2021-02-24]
CADs/V2 - HS422/Rod End/Rod End Housing.SLDPRT
8.99 x 19.9 x 5.90 mm

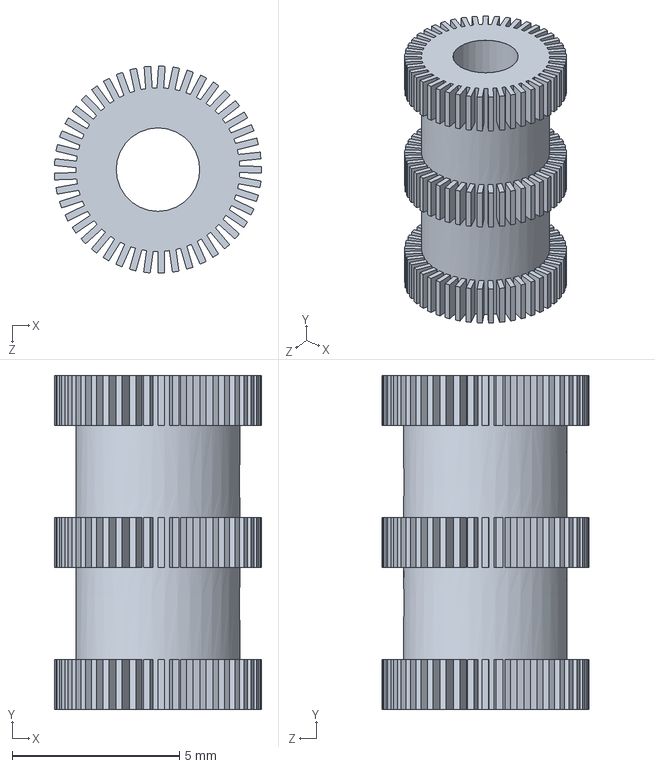
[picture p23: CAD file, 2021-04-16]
CADs/V2 - HS422/Hardware/Threaded insert M3x10x5.SLDPRT
6.21 x 10.0 x 6.21 mm

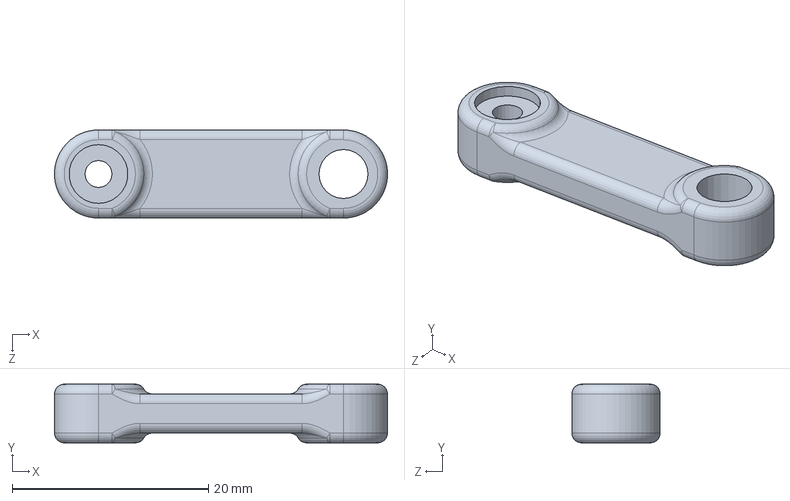
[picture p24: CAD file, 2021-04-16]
CADs/V2 - HS422/ServoArm.SLDPRT
34.0 x 6.00 x 9.00 mm

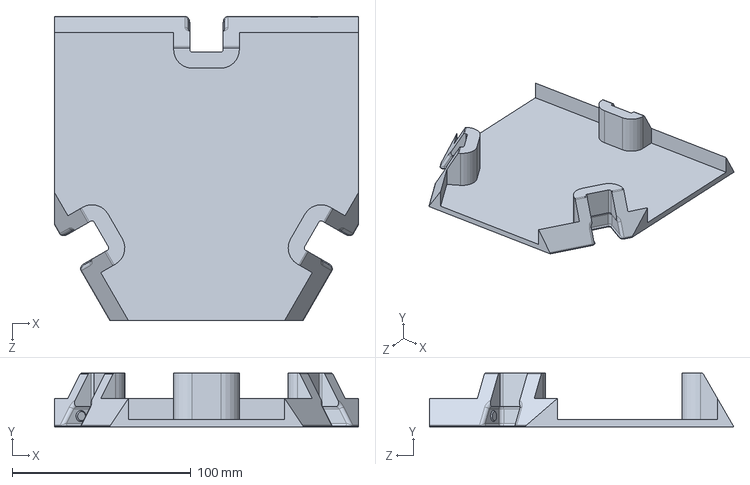
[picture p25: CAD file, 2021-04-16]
CADs/V2 - HS422/MicroController Holder.SLDPRT
170.0 x 30.0 x 170.0 mm

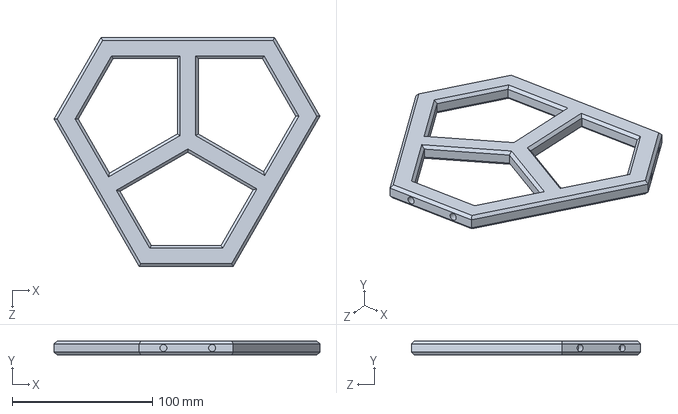
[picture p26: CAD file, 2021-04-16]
CADs/V2 - HS422/Platform.SLDPRT
189.4 x 10.0 x 163.0 mm

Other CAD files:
CADs/V2 - HS422/Base V3-Split.SLDPRT
CADs/V2 - HS422/Tige filetée.SLDPRT
CADs/V2 - HS422/Hardware/91294A134_BLACK ALLOY STEEL FLAT-HEAD SOCKET CAP SCREW.SLDPRT
CADs/V2 - HS422/Hardware/M3x12 - 91294A132_BLACK ALLOY STEEL FLAT-HEAD SOCKET CAP SCREW.SLDPRT
CADs/V1 - SG90 - Deprecated/3mf files/Base.3MF
CADs/V1 - SG90 - Deprecated/3mf files/Fixation Servo Ball joint.3MF
CADs/V1 - SG90 - Deprecated/3mf files/Platform.3MF
CADs/V1 - SG90 - Deprecated/Base.SLDPRT
CADs/V1 - SG90 - Deprecated/Fixation Servo Ball joint.SLDPRT
CADs/V1 - SG90 - Deprecated/Flanged Hex Screw.SLDPRT
CADs/V1 - SG90 - Deprecated/Legs.SLDASM
CADs/V1 - SG90 - Deprecated/Platform.SLDPRT
CADs/V1 - SG90 - Deprecated/ServoMotor.SLDASM
CADs/V1 - SG90 - Deprecated/Stewart Platform.SLDASM
CADs/V1 - SG90 - Deprecated/Tige filetée.SLDPRT
CADs/V1 - SG90 - Deprecated/microservoArm.SLDPRT
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

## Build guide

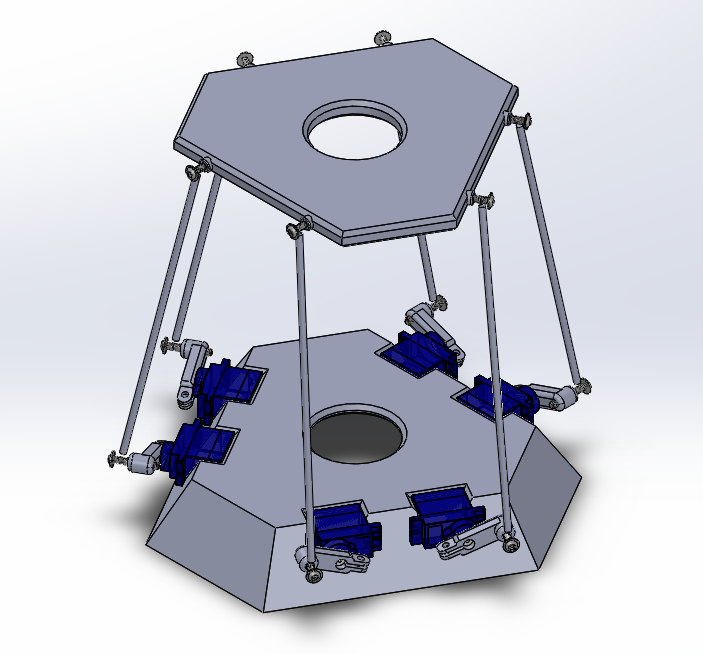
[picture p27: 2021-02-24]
Documentation/img/Assembly.png

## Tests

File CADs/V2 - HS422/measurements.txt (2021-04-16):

"A"= .780
"B"= .530
"C"= 1.33
"D"= .400
"E"= .380
"F"= 1.19
"G"= .460
"H"= 1.05
"J"= 2.08
"K"= .368
"L"= .172
"M"= 1.57

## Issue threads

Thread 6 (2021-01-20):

Power

NoemyCote, 2021-01-20:
Determinate specifications for the power supply (voltage conversion AC->DC, maximum current) and find the power supply. If necessary find relay boards and fuses for security.

NoemyCote, 2021-01-27:
2h30 done Noémy
[https://app.zenhub.com/files/329744338/18281816-dd2c-4c81-b559-97513007a873/download](https://app.zenhub.com/files/329744338/18281816-dd2c-4c81-b559-97513007a873/download)

Closed 2021-02-10.

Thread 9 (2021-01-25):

First CAD design

Jean-GabrielM, 2021-01-25:
First design with our dimensions. Might not be working in its full envelope.  Full assembly.

Jean-GabrielM, 2021-01-25:
Details & files found on Teams Channel Team 5.

Closed 2021-01-25.

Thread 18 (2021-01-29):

Create Python code to control Arduino

xxdroftartsxx, 2021-01-29:
Since we eventually want the Raspberry Pi to control the Arduino, we will need to create that communication and control.

This issue will influence the control implementation into the GUI.

Closed 2021-02-10.

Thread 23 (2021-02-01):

3D print platform V1.0

Jean-GabrielM, 2021-02-01:
Print platform to test that ordered components fit well and see if there are design flaws or problems with components (motor torque, ball joint friction, etc).

Closed 2021-02-02.

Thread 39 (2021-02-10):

Look if the motor HS-422 can replace the motor SG51R

NoemyCote, 2021-02-10:
1. Look at the maximum power current consumption for the 6 servo HS-422 and compare with the adaptator chosen precedently
2. Look at the maximum PWM current consumption for the 6 servo  HS-422 separetly and aditionately
      => Compare one motor with the 20mA PWM output pin and the addition with 800mA.

NoemyCote, 2021-02-22:
The motors can be chaged, but we will need a new adaptor
[https://app.zenhub.com/files/329744338/62fa1edc-014e-4962-8ddf-d5f5f3f2d7cc/download](https://app.zenhub.com/files/329744338/62fa1edc-014e-4962-8ddf-d5f5f3f2d7cc/download)

Closed 2021-02-22.

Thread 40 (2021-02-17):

Platform V2 CAD (HS422)

Jean-GabrielM, 2021-02-17:
The user will now have a new base allowing to fix bigger and stronger servo motors.

Build a base that can support new servo motors.
Add holes to pass wires.
Add brackets to hold motors in the z-axis.

Closed 2021-03-09.

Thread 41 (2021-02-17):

Print & Assemble Platform V2

Jean-GabrielM, 2021-02-17:
The user will now have a new base allowing to fix bigger and stronger servo motors.

Print platform V2. Test that everything fits.
Hopefully ready for release #1.
If supplying the power necessary is problematic --> After release #1.

Closed 2021-03-17.

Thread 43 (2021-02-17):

Calcul du déplacement minimal en z

Jean-GabrielM, 2021-02-17:
Will define the platform accuracy when moving.

Jean-GabrielM, 2021-02-17:
From home, a shift in the angle of 0.76 deg (highest precision given 8bits PWM) with a leg length of 150 mm and servo arms of 16 mm would result in a maximum precision of about 0.21 mm in z-axis movement.
that being said, it is on the low end since the leg is in the plane of the servo arm rotation.

Closed 2021-02-17.

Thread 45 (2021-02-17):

Change Arduino's PWM pins from 8-Bit to 16-Bit resolution

nadwo, 2021-02-17:
As a user, I need to be able to precisely control the angle I send as a command to my servo motors. The current problem lies in the way we send the angle to the servo. Arduino's servo library offers us two options, write() which only takes integer angles and writeMicroSeconds() which takes way more possible angles by taking values in microseconds. This is still not enough as our 8 bit resolution caps us at 2^8 = 256 possible angles. So, we need to upgrade our resolution to 16 bit, which is possible for 8 PWM pins on an Arduino MEGA 2560.

nadwo, 2021-02-23:
I wrote the right functions to allow us to use our PWM pins at 16 bit resolution, but we still need to implement with the python code that sends angles, which is going to need us to change which pins we use so we use those which can be used with 16 bit resolution.

Closed 2021-02-23.

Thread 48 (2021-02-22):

Look with the university to buy the adaptor for powered the HS-422 motors

NoemyCote, 2021-02-22:

NoemyCote, 2021-02-23:
[https://app.zenhub.com/files/329744338/71188d91-b34d-4caf-8e90-85310376aaf7/download](https://app.zenhub.com/files/329744338/71188d91-b34d-4caf-8e90-85310376aaf7/download)
Look with the university for buying it

Closed 2021-03-09.

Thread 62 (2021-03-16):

Update and integrate python file for communication with Arduino

nadwo, 2021-03-16:
As a user, I need to be able to easily command the platform through its inverse kinematics program so I can set the position I want the platform in. To do so, the inverse kinematics program and the motor control program need to be integrated. So we will, update the motor control program in order to import what is necessary from the inverse kinematics program.

nadwo, 2021-03-17:
As a developer, the way I chose to implement this is to change the python communication and motor control program into a class that will be imported in the inverse kinematics and make sure we can send it all of the angles calculated from the waypoints with the inverse kinematics function.

Closed 2021-03-17.

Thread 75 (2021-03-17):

look if the BreadBoard is correct with 6A,5V

NoemyCote, 2021-03-17:

NoemyCote, 2021-03-17:
[Uploading... Transition_wire_and_protoboard.pdf]

NoemyCote, 2021-03-17:
[https://app.zenhub.com/files/329744338/89ba3319-b910-4c4a-aa69-361dc94b3f86/download](https://app.zenhub.com/files/329744338/89ba3319-b910-4c4a-aa69-361dc94b3f86/download)

Closed 2021-03-24.

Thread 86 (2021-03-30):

Fix anchor position of platform for the plot and limit displacement when angles give NaN

davidtrepanier, 2021-03-30:
Fix update anchors positions in global (Base) frame. Create function for servo angles. Limit displacement to enveloppe (while updating origin & vectorBase).

Closed 2021-03-31.

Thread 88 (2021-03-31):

Refactor Arduino communication class

nadwo, 2021-03-31:
As a user, I need to be able to use the Arduino communication class to easily send all the angles I want to the motors so they follow the wanted trajectory. To do so, we need to correct the Arduino communication class so the sendAngles function takes arrays of the form myArray[n][6] and takes angles in radians while sending degrees to the motors.

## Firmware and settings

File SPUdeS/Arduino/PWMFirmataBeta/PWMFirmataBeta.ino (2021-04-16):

/*
 * Firmata is a generic protocol for communicating with microcontrollers
 * from software on a host computer. It is intended to work with
 * any host computer software package.
 *
 * To download a host software package, please click on the following link
 * to open the list of Firmata client libraries in your default browser.
 *
 * https://github.com/firmata/arduino#firmata-client-libraries
 */

/* Supports as many analog inputs and analog PWM outputs as possible.
 *
 * This example code is in the public domain.
 */
#include <Firmata.h>

byte analogPin = 0;
const byte pwm0pin = 11;     // PB5, OC1A
const byte pwm1pin = 12;     // PB6, OC1B
const byte pwm2pin = 5;      // PE5, OC3A
const byte pwm3pin = 2;      // PE4, OC3B
const byte pwm4pin = 3;      // PE5, OC3C
const byte pwm5pin = 6;      // PH3, OC4A
const byte pwm6pin = 7;      // PH4, OC4B
const byte pwm7pin = 8;      // PH5, OC4C
const byte pwm8pin = 46;     // PL3, OC5A
const byte pwm9pin = 45;    // PL4, OC5B
const byte pwm10pin = 44;    // PL5, OC5C

const uint16_t MAX_PWM_VALUE = 65535U;

//----------------------------------------------------------------------------------------------------
// Setup timers for 16 bit PWM
void initPWM() {
  noInterrupts();

  TCCR3A = 1 << WGM31 | 1 << COM3A1 | 1 << COM3B1 | 1 << COM3C1; // set on top, clear OC on compare match
  TCCR3B = 1 << CS30  | 1 << WGM32 | 1 << WGM33;   // clk/1, mode 14 fast PWM
  TCCR4A = 1 << WGM41 | 1 << COM4A1 | 1 << COM4B1 | 1 << COM4C1; // set on top, clear OC on compare match
  TCCR4B = 1 << CS40  | 1 << WGM42 | 1 << WGM43;   // clk/1, mode 14 fast PWM
  TCCR5A = 1 << WGM51 | 1 << COM5A1 | 1 << COM5B1 | 1 << COM5C1; // set on top, clear OC on compare match
  TCCR5B = 1 << CS50  | 1 << WGM52 | 1 << WGM53;   // clk/1, mode 14 fast PWM
  ICR3 = MAX_PWM_VALUE;
  ICR4 = MAX_PWM_VALUE;
  ICR5 = MAX_PWM_VALUE;

  interrupts();
  pinMode(pwm0pin, OUTPUT);
  pinMode(pwm1pin, OUTPUT);
  pinMode(pwm2pin, OUTPUT);
  pinMode(pwm3pin, OUTPUT);
  pinMode(pwm4pin, OUTPUT);
  pinMode(pwm5pin, OUTPUT);
  pinMode(pwm6pin, OUTPUT);
  pinMode(pwm7pin, OUTPUT);
  pinMode(pwm8pin, OUTPUT);
  pinMode(pwm9pin, OUTPUT);
  pinMode(pwm10pin, OUTPUT);

}

//----------------------------------------------------------------------------------------------------
// Set a 16 bit PWM value for a channel
void setPWM(byte no, uint16_t pwm) {
  noInterrupts();
  switch (no) {
    case 0 :
      OCR1A = pwm;
      break;
    case 1 :
      OCR1B = pwm;
      break;
    case 2 :
      OCR3A = pwm;
      break;
    case 3 :
      OCR3B = pwm;
      break;
    case 4 :
      OCR3C = pwm;
      break;
    case 5 :
      OCR4A = pwm;
      break;
    case 6 :
      OCR4B = pwm;
      break;
    case 7 :
      OCR4C = pwm;
      break;
    case 8 :
      OCR5A = pwm;
      break;
    case 9 :
      OCR5B = pwm;
      break;
    case 10 :
      OCR5C = pwm;

  }
  interrupts();
}

void analogWriteCallback(byte pin, int value)
{
  if (IS_PIN_PWM(pin)) {
    pinMode(PIN_TO_DIGITAL(pin), OUTPUT);
    //analogWrite(PIN_TO_PWM(pin), value);
    setPWM(PIN_TO_PWM(pin), map(value, 0, 180, 0,MAX_PWM_VALUE));
  }
}

void setup()
{
  initPWM();
  Firmata.setFirmwareVersion(FIRMATA_FIRMWARE_MAJOR_VERSION, FIRMATA_FIRMWARE_MINOR_VERSION);
  Firmata.attach(ANALOG_MESSAGE, analogWriteCallback);
  Firmata.begin(57600);

}

void loop()
{
  while (Firmata.available()) {
    Firmata.processInput();
  }
  // do one analogRead per loop, so if PC is sending a lot of
  // analog write messages, we will only delay 1 analogRead
  Firmata.sendAnalog(analogPin, analogRead(analogPin));
  analogPin = analogPin + 1;
  if (analogPin >= TOTAL_ANALOG_PINS) analogPin = 0;
}

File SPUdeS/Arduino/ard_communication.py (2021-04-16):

"""This file handles the motor functions to send to Arduino. It uses a library called pyfirmata to communicate with the Arduino and implements ino language.
The functions declared here are used in the Server.py file."""
import pyfirmata
from time import sleep

class ard_communication:
    """The ard_communication class handles all the communication protocol between the Arduino and the Python
    functions using the library pyfirmata. """

    def __init__(self):
        """ The __init__() function sets up the connection to the Arduino via USB, it initializes the Motor to Pin
        connections and some basic set up angles (min, max, homing angles). This function also calls the
        setUpMotors() function to initialize the motor connections with the Arduino. It finally calls the
        gotoHomePosition() function which sends the homing angles command to the motors. """
        self.board = pyfirmata.Arduino('COM3')  # RPI: '/dev/ttyACM0'
        self.alpha0 = -2.7
        self.homingAngle = [[90+self.alpha0, 90+self.alpha0, 90+self.alpha0,
                            90+self.alpha0, 90+self.alpha0, 90+self.alpha0]]
        # Assign a pin number to each motor
        self.motor1 = 7
        self.motor2 = 9
        self.motor3 = 11
        self.motor4 = 12
        self.motor5 = 5
        self.motor6 = 3
        self.max_angle = 180
        self.min_angle = 0
        self.setUpMotors()
        self.goToHomePosition()

    def setUpMotors(self):
        """The setUpMotors() function initializes the pin connections to the servo motors."""
        self.board.digital[self.motor1].mode = pyfirmata.SERVO
        self.board.digital[self.motor2].mode = pyfirmata.SERVO
        self.board.digital[self.motor3].mode = pyfirmata.SERVO
        self.board.digital[self.motor4].mode = pyfirmata.SERVO
        self.board.digital[self.motor5].mode = pyfirmata.SERVO
        self.board.digital[self.motor6].mode = pyfirmata.SERVO

    def setServoAngle(self, angle, isRad=1):
        """The setServoAngle() function receives a set of arrays with each 6 elements. The sets of angles are for
        sending small movements to the motors and the 6 elements in each array are the angles for each one of the
        motors. There is also an option for sending the list of angle arrays in radian or not. By default,
        we assume that the angles are in radians. """
        if isRad:
            rad_to_deg = 180.0/3.1416
            alpha = 90
        else:
            rad_to_deg = 1
            alpha = 0

        for i in range(len(angle)):
            self.board.digital[self.motor1].write(int(alpha + angle[i][0] * rad_to_deg))
            self.board.digital[self.motor2].write(int(180.0 - (alpha + angle[i][1] * rad_to_deg)))
            self.board.digital[self.motor3].write(int(alpha + angle[i][2] * rad_to_deg))
            self.board.digital[self.motor4].write(int(180.0 - (alpha + angle[i][3] * rad_to_deg)))
            self.board.digital[self.motor5].write(int(alpha + angle[i][4] * rad_to_deg))
            self.board.digital[self.motor6].write(int(180.0 - (alpha + angle[i][5] * rad_to_deg)))
            sleep(0.01)

    def goToHomePosition(self):
        """The goToHomePosition() function calls the setServoAngle() function with the arguments of the homing angles
        initialized in the __init__(). """
        self.setServoAngle(self.homingAngle, 0)
        print("HOMING NOW")

if __name__ == "__main__":
    arduino_coms = ard_communication()

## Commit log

2021-01-27 Definition of all points of the base & servos.
2021-01-29 made a triangle button that alerts when pressed
2021-01-29 Made triangular button that alerts when pressed
2021-02-03 Add code for arduino_motors on arduino only
2021-02-08 Testing a Javascript function for button actions
2021-02-10 First implemantaion of servo motor control with arduino through serail communication with raspberry Pi
2021-02-10 First implementation of a Qt Creator interface that lets us send the wanted angles to arduino through serial communication and JSON messages
2021-02-10 Revert "First implementation of a Qt Creator interface that lets us send the wanted angles to arduino through serial communication and JSON messages"
    This reverts commit 7977f2acffdd07bd8674b278d2e76f4a944c2372.
2021-02-10 First implementation of a Qt interface that lets us send JSON message to arduino about the wanted angles for our servoMotors through serial communication, in the appropriate branch
2021-02-10 Set up motor communication between arduino and python code. Using Lib called Firmata.
2021-02-10 Adding py to arduino comminication code
2021-02-10 *Correction - Now adding py to arduino code
    [StandardFirmata.ino]
2021-02-10 Setting up for review of buttons
2021-02-10 Set up code for 6 servo motors to move when given an angle. Set an arbitrary homing position and a up-down position function
2021-02-10 Fixed bug in function to activate motors
2021-02-13 Modifying interface buttons and arduino connectivity
2021-02-13 Adding a way to input the angle for the servo motors into the interface
2021-02-19 Resolved issue with denied 'COM3' port access. Request from web page to server is being received code 200. However, the servo motors only buzz. None have moved yet
    [ard_communication.py]
2021-02-19 Resolved issue of servo buzzing or freaking out. It was a hardware issue not a software issue. Forgot cable from ground to GND of Arduino
    [ard_communication.py]
2021-02-20 Inverse kinematics code cleanup
2021-02-22 Create stewartPlatform, _platform, _base, _piece, frame classes to define stewart platform. Inverse kinematics
2021-02-23 Changes for adding a button for homing. So the button request doesn't work (error 400). Need to add some formatting as well.
    [ard_communication.py]
2021-02-23 Added a button for upward sweep servo movement. Not fully functional
2021-02-23 Implementation of the first version of motor control with 16 bit PWM resolution, in a separate file which could be used eventually instead of the standardFirmata, which does too much for our usage.
2021-02-23 Revert "Implementation of the first version of motor control with 16 bit PWM resolution, in a separate file which could be used eventually instead of the standardFirmata, which does too much for our 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
    This reverts commit 82c20a6dfb3d42549a4bc6dda93e9822bcc205b4.
2021-02-23 Version #1 CAD Stewart Platform
    [ArduinoMega.SLDPRT, Base.3MF, Base.SLDPRT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]
2021-02-23 Commit of the right version of the first implementation of the motor control with 16 bit resolution PWM
2021-02-28 Version #2 CAD platform - HS422 motors.
    [91294A134_BLACK ALLOY STEEL FLAT-HEAD SOCKET CAP SCREW.SLDPRT, ArduinoMega.SLDPRT, Base.3MF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]
2021-02-28 Reorganise files of 1st design in folder V1-SG90.
    [ArduinoMega.SLDPRT, Base.3MF, Base.SLDPRT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]
2021-03-02 Modofications servo_arm & ajout fichier d'impression (gcode).
    [ServoArm.SLDPRT]
2021-03-16 FInally got buttons to the left of video feed
2021-03-17 Updating our python motor control program into a class that can be imported in our main as an object
2021-03-17 Quick correction to ard_communication class
    [ard_communication.py]
2021-03-17 Web page app commit error fix
    [ard_communication.py]
2021-03-18 Update servo angle at init
2021-03-24 Refactor kinematicFunctions, stewartClasses, inverse kinematics
2021-03-27 Latest 3D printing files.
    [Base.SLDPRT, BaseSplit.3MF, Base_Split.SLDPRT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]
2021-03-27 Remove suspicious file (cad RPi)
2021-03-29 Plot function & resolve anchor numbering.
    [stewartPlatform.py]
2021-03-30 Fix update anchors positions in global (Base) frame. Create function for servo angles. Limit displacement to enveloppe (while updating origin & vectorBase).
    [stewartPlatform.py]
2021-03-30 Refactor plot method, pathSampling method. Bug fix
    [stewartPlatform.py]
2021-03-31 Changes to the arduino communication class so it takes arrays of form array[n][6] so it works with inverse kinematics code
2021-03-31 Updated the goToHomePosition function as well as the homingAngle variable, updated sendAngles function so it works with inverse kinematics program, included first pre-defined trajectories
2021-03-31 Changes for sending JSON input to kinematic functions
2021-03-31 Base V3 - Split & Base V3
    [Base V3-Split.SLDPRT, Base V3.SLDPRT]
2021-04-01 Ajout pièce MicroController Holder. Modification de l'assemblage pour inclure holder & changement de pièce pour la base.
    [91294A134_BLACK ALLOY STEEL FLAT-HEAD SOCKET CAP SCREW.SLDPRT, ArduinoMega.SLDPRT, Base.SLDPRT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]
2021-04-01 Remove usless arduino code and replace it with actual arduino code
    [StandardFirmata.ino, ard_communication.py]
2021-04-01 Remove arduino_comms code from PythonUI folder
2021-04-01 3D printing file holder
    [MicroController Holder.3MF]
2021-04-02 Continuing adding sweep buttons and using the plotted image in UI.
2021-04-07 Bug fix in confirmRequestValidity and update todos in SP flask request sequence
    [stewartPlatform.py]
2021-04-07 Add option to change camera on the UI
2021-04-07 Update "Change Camera" button
2021-04-07 Change position button sizes
2021-04-08 Many updates and bug fixes to have everything work together
    [ard_communication.py, stewartPlatform.py]
2021-04-14 Fixing typos in README and correcting setServo angle function for data in rads
    [ard_communication.py]
2021-04-14 Changed buttons alpha...
2021-04-15 Add the motor control documentation to the READ.me and add our beta version of the PWMFirmata.ino file for future reference
2021-04-15 commit for arduino com port and readme section UI
2021-04-15 Add software installation in readme, change pin to motors in ard_coms and change requirements.txt
2021-04-16 Adding doc string to the Arduino .py files
2021-04-16 Adding doc string to head of Arduino file
2021-04-16 Update Rods and heim joints in readme

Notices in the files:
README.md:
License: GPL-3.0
